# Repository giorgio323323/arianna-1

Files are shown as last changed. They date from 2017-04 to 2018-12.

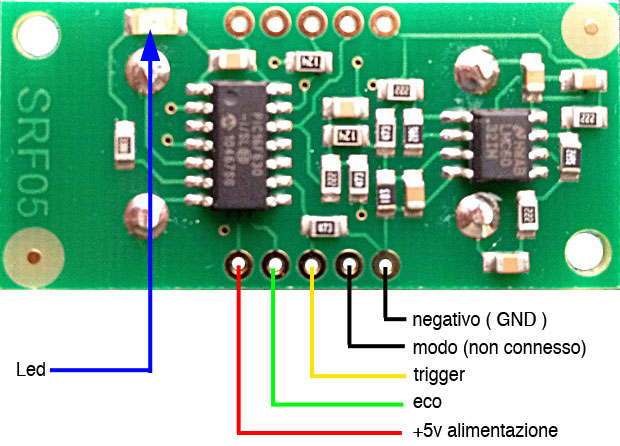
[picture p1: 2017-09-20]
hw/sensore-ad-ultrasuoni-srf.05jpg.jpg

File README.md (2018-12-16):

# Arianna
Arianna: il robot biblitecario.

il progetto è stato portato in: https://github.com/giorgio323323/ARI_V3

## Introduzione

Da [Arianna by CSBNO](http://webopac.csbno.net/library/Canegrate/makers-lab/arianna/) :
> Arrivo in biblioteca e chiedo “Robinia Blues” di Valter Binaghi, il bibliotecario consulta il computer e mi informa che c’è e lo posso trovare tra gli autori italiani. Un attimo di imbarazzo, non frequento questo luogo abbastanza da conoscere la disposizione degli scaffali, faccio per domandare ma il mio interlocutore mi anticipa dicendomi di seguire Arianna. Arianna? Un sibilo mi fa voltare, vedo una macchinina che parte lungo il corridoio, porta la scritta Arianna. Al mio sguardo interrogativo il mio interlocutore mi fa cenno di andare, segua Arianna mi dice. Tutto dura pochi secondi nei quali valuto anche la possibilità di essere vittima di “Scherzi a parte”, Arianna si ferma, si gira un poco e con un altro fruscio un puntatore luminoso si muove, si accende e quando decido di guardare dove Arianna sembra “indicare” vedo una luce sui libri e li vicino il mio “Robina Blues”. Lo prendo, lo sfoglio e me ne vado un poco stupito, saluto il bibliotecario e nel frattempo risento il sibilo. Vedo Arianna che torna da dove era venuta, la vedo accoccolarsi in una piccola casetta e io lascio la biblioteca pronto a rileggere il libro di un bravo insegnante che ha attraversato i nostri luoghi.

## Obiettivo 
La costruzione di un robot ***autonomo*** ed ***indipendente*** con lo scopo di accompagnare una persona al libro richiesto. La navigazione avviene in un ambiente dinamico dove anche i singli scaffali possono cambiare di posizione.

## Roadmap

- [x] Start
- [x] Primi prototipi (Ambros,Arianna,4rianna,..)
- Struttura
    - [ ] Arianna
    - [ ] Ambros
    - [ ] 4rianna
    - [ ] ..
- Movimento
    - [ ] Motori DC
    - [x] Stepper
    - [ ] Altro
- Altro
- [ ] Interazione biblio DB

## Contatti
[STUFFcube](https://stuffcube.wordpress.com/)

## License

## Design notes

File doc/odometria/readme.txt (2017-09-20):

Introduction to the files in the Kalman filter simulator .zip file.

After you have unpacked the .zip file you have obtained a directory that contains the Matlab simulator functions that I've used in my thesis on Robot Localization and Kalman Filters. All plots presented in the thesis are generated using the functionality of the simulator.

The simulator does not have a graphical user interface. You will have to look into the different function files to get to know the workings of the simulator, although I don't think that that will give many problems. 

charts/ contains functions to plot charts when data is generated
diff_drive/ contains the truth and KF model that implement the drive system and sensor models from the thesis. In particular, diff_drive_problem.m defines the estimation problem. This file is documented with comments on how to use the file.
kf_methods/ contains functions that implement different KFs
misc/ contains miscalaneous functions needed by the simulator
track_drive_single_and_multiple/ contains the models used when detecting single or multiple landmarks at the same time

To get started, make sure that the pathdef.m includes the subdirectories in this directory. 
Then either run 'demo_fs_ekf' (extended Kalman Filter) or 'demo_fs_iekf' (iterated extended Kalman filter).

To get to know the simulator, it is easiest to try the above commands and step through each line of the code. I have added commentry to the code to make it more understandable. However, if you have questions, feel free to contact me via http://contact.negenborn.net/.

Rudy Negenborn
http://www.negenborn.net/

August 2003
July 2009 (update)

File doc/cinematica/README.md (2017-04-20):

# Cinematica

Qui puoi trovare i contenuti per la gestione del movimento dei motori di [Arianna].
>La cinematca è quel ramo della meccanica che si occupa di descrivere quantitativamente il moto dei corpi, indipendentemente dalle cause del moto stesso.

In pratica qui vengono approfonditi come muovere arianna, nonchè formule e ragionamenti che hanno portato a certe soluzioni.

Qui si trovano file per la gestione dei movimenti attraverso motori. Per ora viene contemplato solo l'utilizzo di motori stepper, in futuro verranno mergiati nuovi esempi con motori DC.

#Obiettivi
- [x] Init
- [ ] Gestione degli stepper
  - [x] Gestione accelerazione e velocità (tramite [https://github.com/adafruit/AccelStepper](AccellStep by LadyAda)
  - [x] Buy ingredients
  - [ ] Cook recipe
- [ ] Sleep

# Esempi

La seguente cartella contiene alcuni esempi di utilizzo di stepper con alcune librerie vedi
  - Import a HTML file and watch it magically convert to Markdown
  - Drag and drop images (requires your Dropbox account be linked)

#Dipendenze

Attenzione!
Il seguente codice riporta delle dipendenze, installale o verifica la presenza nel tuo ambiente prima di compilare il codice.

| Dipendenza | IDE |
| --- | --- |
| [AccelStepper](https://github.com/adafruit/AccelStepper) | Arduino |
| [AFMotor](https://github.com/adafruit/Adafruit-Motor-Shield-library) | Arduino |

Tips:
  - Installa scaricando la repo da Zip, si fa prima ;).

### Todos

License
----

MIT

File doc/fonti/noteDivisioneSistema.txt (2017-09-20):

note sulla divisione del sistema Arianna

il sistema è suddiviso su tre parti logiche e volendo anche hardware

lo chiamo Attuatore, anche se il termine può essere improprio: 
	si occupa della gestione dei sensori e degli attuatori. 
	
	un Arduino controlla la velocità, direzione, misura lo spostamento delle ruote.
	legge i sensori di distanza dagli oggetti.
	governa il sensore di puntamento del libro.
	restituisce informazioni sul suo stato.

	ha delle funzioni primitive che vengono comandate via seriale da un livello superiore

	ho trovato che delle primitive utili sono:

		movimento con arresto al superamento della Distanza obbiettivo
			il movimento può essere:
				con direzione imposta dal supervisore scrivendo angolo di sterzo 
				con direzione controllata in modo da stare a a una certa distanza dalla
				parete sx o dx. Il controllo regola lo sterzo
				per mantenere la parete a una certa distanza.
		
		definire la velocità di crociera
		definire la distanza da percorrere
		
		nel mio caso ho montato un sensore a ultrasuoni sul frontale. Posso ruotarlo
		a piacere con un servo (PAN). da qui i comandi A e m.
		Sul PAN c'è un servo che fa il TILT del puntatore.
		Giunti allo scaffale il robot arretra curvando per allontanarsi dallo scaffale.
		L'incertezza della fermata la correggo effettuando delle misure della distanza
		dalla libreria, la minima distanza indica che il sensore (PAN) è perpendicolare.
		In base alla distanza dalla libreria e all'altezza del ripiano calcolo l'angolo
		di TILT e così posso puntare.
		
		lo script farebbe:
		riceve dati da Interfaccia (vedi sotto)
		comando moto con sensore sx per una distanza D = Dscaffale
		all'arresto moto con sterzo imposto e distanza D = -distanza di arrestramento
		algortimo di ricerca m minima in funzione dell'angolo
		invio angolo di TILT in funzione di m trovata e altezza ripiano
		accendi puntatore
		
		voilà, le jeux sont fait

			S Scrivo sterzo e suo angolo						[gradi] 90 diritto 
																		180 dx
																		0   sx
			D scrivo distanza relativa da percorrere e valore 	[mm]
			d lettura distanza assoluta (odometro)				[mm]
			V scrivo setpoint velocita' con valore motorSpeedValue
			v leggo velocità (motorSpeedRef)
			e errore
			l libero (viaLibera) stato sensore anteriore
			r statoRun	
			R statoRun (scrivi) 0: fermo, 1: controllo con sensore dx, 2: sterzo esterno
			  si ferma al superamento quando odometro supera la D attiva 
			A angolo sonar
			m misura con sonar [cm]

Supervisore, anche questo termine può essere rivisto: 
	tramite seriale comanda le primitive dell'attuatore per comporle in movimenti organici e complessi.
	riceve indicazioni su cosa fare dall'Interfaccia con la biblioteca

Interfaccia, è un software che gira sul pc della biblioteca. 
	A partire dal codice del libro interroga il dataBase che restituisce un record contenente:
	numero scaffale
	numero ripiano
	posizione x, y, z del centro del ripiano dove giace il libro
	
	Passa queste informazioni al SUpervisore.
	
	questo DB deve essere popolando manualemnte censendo i ripiani della biblioteca e individuando il libri 
	posti agli estremi del ripiano.
	
	il nostro scopo non è puntare il libro ma il ripiano che lo contiene.

La comunicazione tra Attuatore e Supervisore

	Avviene tramite seriale. Indipendentemente da come verrà fatto il supervisore (Raspberry, ESP, altro) 
	ho trovato comoda una interfaccia a misura "umana", cioè con stringhe di comando mnemoniche, un poco tipo
	Gcode. Questo permette di testare il sistema con una interfaccia seriale testuale (es quella nell'IDE
	di Arduino).
	Dispone di un semplice l'acknowledge di ricezione comando e un timeout.
	
	Sul supervisore si possono realizzare dei semplici script che sfruttano le funzioni base per
	farne di complesse.
	
	Se concordiamo di renderla comune possiamo condividere diverse cose. 
	
	metto in fondo lo snippet di codice che la realizza e descrive:

// 

	/*
	verifica se arrivano caratteri da seriale
	considero un pacchetto con la forma char1 (comando) seguito da un eventuale parametro
	In maiscolo i valori che scrivo
	in minuscolo quelli che leggo
	
	char 1:	parametro modificato, 
			S Scrivo sterzo e suo angolo						[gradi] 90 diritto 
																		180 dx
																		0   sx
			D scrivo distanza relativa da percorrere e valore 	[mm]
			d lettura distanza assoluta (odometro)				[mm]
			V scrivo setpoint velocita' con valore motorSpeedValue
			v leggo velocità (motorSpeedRef)
			e errore
			l libero (viaLibera) stato sensore anteriore
			r statoRun	
			R statoRun (scrivi) 0: fermo, 1: controllo con sensore dx, 2: sterzo esterno
			  si ferma al superamento quando odometro supera la D attiva 
			A angolo sonar
			m misura con sonar [cm]

*/

void getCmd(void){
static float x, y;
static char smComandi = 0;
static char inCmd;
static unsigned long time, cmdTime;

	// se il pacchetto non arriva completo in un secondo 
	// resetto ricezione
	if ((smComandi != 0) && ((millis() - cmdTime) > 1000 )) {
		Serial.println('Timeout');
		smComandi = 0;
	}

	if (Serial.available() > 0) {

		switch (smComandi) {
			case 0: // attesa 1rst valore

				inCmd = Serial.read();
				cmdTime = millis();
				
				switch (inCmd) {
		
					// scrivo valore
					case 'S': 
					case 'D': 
					case 'R': 
					case 'V': 
					case 'A': 
							smComandi = 1;		// stato a seconda del numero di
												// parametri da ricevere
						break;
		
					case 'd': 
					case 'e': 
					case 'v': 
					case 'l': 
					case 'r': 
					case 'm': 
							smComandi = 2;		// stato a seconda del numero di
												// parametri da ricevere
												// questa è lettura quindi segue subito risposta
						break;
				}
				break;
			case 1: // attende 1 valore
				// look for the next valid integer in the incoming serial stream:
				x = Serial.parseInt();
				smComandi = 2; 	// mette in esecuzione valore
				break;	
				
			case 2: // attesa terminatore

				if (Serial.read() != '\n') break;
				
				switch (inCmd) {
					case 'S': 
							angoloSterzo = x;
							smComandi = 0;		
							Serial.print("S: ");
							Serial.println(angoloSterzo);
						break;
		
					case 'D': 
							distanza += x;
							smComandi = 0;		
							Serial.print("D: ");
							Serial.println(distanza);
						break;
		
					case 'R': 
							statoRun = x;
							smComandi = 0;		
							Serial.print("R: ");
							Serial.println(statoRun);
						break;

					case 'V': 
							motorSpeedValue = x;
							smComandi = 0;		
							Serial.print("V: ");
							Serial.println(motorSpeedValue);
						break;
		
					case 'A': 
							sonarAngle = x;
							smComandi = 0;		
							Serial.print("A: ");
							Serial.println(sonarAngle);
						break;
		
					case 'd': 
							smComandi = 0;		
							Serial.print("d: ");
							Serial.println(odometro);
						break;
		
					case 'e': 
							smComandi = 0;		
							Serial.print("e: ");
							Serial.println(errore);
						break;
		
					case 'v': 
							smComandi = 0;		
							Serial.print("v: ");
							Serial.println(motorSpeed);
						break;

					case 'l': 
							smComandi = 0;		
							Serial.print("l: ");
							Serial.println(viaLibera);

					case 'r': 
							smComandi = 0;		
							Serial.print("r: ");
							Serial.println(statoRun);
						break;

					case 'm': 
							smComandi = 0;		
							misura = sonarMisura(5);
							Serial.print("m: ");
							Serial.println(misura);
						break;
				}
				
				break;
			default:
				smComandi = 0;
				break;
		}
		
	}// in serialLine.available
}

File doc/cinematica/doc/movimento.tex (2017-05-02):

\documentclass[12pt,oneside,a4paper]{article}

%% Language and font encodings

\usepackage[english]{babel}
\usepackage[utf8x]{inputenc}
\usepackage[T1]{fontenc}
\usepackage{amssymb,tikz,pdftexcmds,xparse}

%change caption of contents e appendices

\addto\captionsenglish{% Replace "english" with the language you use
	\renewcommand{\figurename}{Figura}%
	\renewcommand{\contentsname}{Table of Contents}%
	\renewcommand{\contentsname}{Contenuti}
}

%% Give you the possibiliy of split text
\usepackage{seqsplit}

%% Sets page size and margins
\usepackage[a4paper,top=3cm,bottom=2cm,left=3cm,right=3cm,marginparwidth=1.75cm]{geometry}

%%allow to break url
\usepackage[hyphens]{url}

%% Useful packages
\usepackage{amsmath}
\usepackage{graphicx}
\graphicspath{ {./immagini/} }
\usepackage[colorinlistoftodos]{todonotes}
\usepackage[colorlinks=true, allcolors=black]{hyperref}
\usepackage{todonotes}
\usepackage{multicol}

%appendice 
\usepackage[toc,page]{appendix}
\renewcommand\appendixtocname{Appendice}
\renewcommand\appendixpagename{Appendice}
%% Personal function

%no label
\usepackage[nolabel, final]{showlabels}

%% Solidity env, per ora è java
\usepackage{listings}
\usepackage{color}

\definecolor{dkgreen}{rgb}{0,0.6,0}
\definecolor{gray}{rgb}{0.5,0.5,0.5}
\definecolor{mauve}{rgb}{0.58,0,0.82}

\lstset{frame=tb,
	language=Java,
	aboveskip=3mm,
	belowskip=3mm,
	showstringspaces=false,
	columns=flexible,
	basicstyle={\small\ttfamily},
	numbers=none,
	numberstyle=\tiny\color{gray},
	keywordstyle=\color{blue},
	commentstyle=\color{dkgreen},
	stringstyle=\color{mauve},
	breaklines=true,
	breakatwhitespace=true,
	tabsize=3
}

	\title{Movimento di un robot 2 motori rear e una sfera front}
	\author{Luca Vecchi - STUFFCUBE}
	\date{20 Aprile 2017}

\begin{document}
	%\input{./Struttura/Frontespizio.tex}

	\maketitle
	\clearpage

	%	\input{Struttura/Introduzione.tex}
	
	\section{Curvatura}
	
	Vogliamo astrarre il movimento di Arianna in due tipologie diverse: rette e circonferenze. Una futura implementazione delle curve bezier (manca di trovare come fare l'offset e di modificare il path) potrà dare una completa gestione dei movimenti potendo controllare anche l'angolo di arrivo al punto.
	
	Possiamo considerare il contenuto informativo di $S_0 \bigcup r_0$ al pari di $\alpha \bigcup r_0$ e $S_0 \bigcup \alpha$ per via delle ovvie uguaglianze.
	Nel nostro caso per le rette andremo a definire la funzione \textit{Retta} come segue:
	retta ($S_0$): $S_s , S_d$
	
	, mentre nel caso delle circonferenze:
	
	circ($\alpha$,$r_o$,$\Delta$):  $S_s , S_d$
	
	dove $\delta$ è la distanza tra il centro del robot e la circonferenza tracciata dal movimento del centro delle ruote.
	
	\begin{equation*}
	S_0 \equiv \alpha * 2 * \pi * r_0 \div 360
	\end{equation*}
	\begin{equation*}
	S_1 \equiv \alpha * 2 * \pi * (r_0 - \Delta) \div 360
	\end{equation*}	
	\begin{equation*}
	S_2 \equiv \alpha * 2 * \pi * (r_0 + \Delta) \div 360
	\end{equation*}
	
	Come si evince dall'immagine \ref{fig:circonferenze} si può notare le circonferenze concentriche, rappresentate dalla più interna verso l'esterna, come il tragitto effettuato dalla ruota più interna, dal centro del robot e dalla ruota più esterna.
	
	La difficoltà sta nella gestione dei motori in modo sincrono in quanto perchè il centro del robot effettui una circonferenza perfetta, la velocità delle ruote deve essere mantenuta costante\footnote{Vedi libreria Accelstepper}.

	\clearpage

	%% Bibliography .bib
	%\bibliography{./Struttura/bib.bib}
	%\bibliographystyle{unsrt}	
\end{document}

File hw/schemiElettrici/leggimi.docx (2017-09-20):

https://www.build-electronic-circuits.com/gerber-file/

HC-06 Bluetooth module

http://42bots.com/tutorials/hc-06-bluetooth-module-datasheet-and-configuration-with-arduino/

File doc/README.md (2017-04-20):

# Testo

Qui si potrebbe inserire un testo riassuntivo per la produzione di un ***pdeffone*** enorme che conterrà tutto il percorso.

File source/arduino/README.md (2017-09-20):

# arianna
arianna: il robot biblitecario

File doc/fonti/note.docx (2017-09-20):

Arrivo in biblioteca e chiedo “Robinia Blues” di Valter Binaghi, il bibliotecario consulta il computer e mi informa che c’è e si trova tra autori italiani. Un attimo di imbarazzo, non frequento questo luogo abbastanza da conoscere la disposizione degli scaffali, faccio per domandare ma il mio interlocutore mi anticipa dicendomi di seguire Arianna. Arianna ? Un sibilo mi fa voltare, vedo una macchinina che parte lungo il corridoio, porta la scritta Arianna. Al mio sguardo interrogativo il mio interlocutore mi fa cenno di andare, segua Arianna mi dice. Tutto dura pochi secondi nei quali valuto anche la possibilità di essere vittima di “Scherzi a parte”, Arianna si ferma, si gira un poco e con un altro fruscio un puntatore luminoso si muove, si accende e quando decido di guardare dove Arianna sembra “indicare” vedo una luce sui libri e li vicino il mio “Robina Blues”. Lo prendo, lo sfoglio e me ne vado perplesso, saluto il bibliotecario e nel frattempo risento il sibilo. Vedo Arianna che torna da dove era venuta, la vedo accoccolarsi in una piccola casetta e io lascio la biblioteca pronto a rileggere il libro di un bravo insegnante che ha attraversato i nostri luoghi.

Arianna è un robot che è in grado di muoversi sul pavimento e andare dove gli viene richiesto. E’ il progetto che abbiamo avviato all’interno di StuffCube. La prima parte è stato definire cosa deve fare, lo abbiamo descritto nell’incipit. Successivamente abbiamo scomposto il progetto nelle diverse funzioni di considerando le caratteristiche della biblioteca che ci ospita:

- Realizzare oggetto che si muove (rover cioè vagabondo)
- sensori sul rover
- ricevimento comandi di destinazione
- determinare dove deve andare
- determinare dove è
- determinare il moto verso la destinazione
- indicare il libro
- ritorno a casa
- ricarica
- mappare gli scaffali quando vengono spostati.

Altri vincoli di progetto che ci siamo dati sono di essere il meno intrusivi possibile, questo fa si che dobbiamo evitare soluzioni che richiedano sorgenti di alimentazione, oppure il porre strisce guida sul pavimento e cosi via.

Inizieremo partendo dagli scaffali più semplici, quelli che affiancano la parete. L’idea è seguire lo scaffale viaggiandoci radente e identificando dove siamo misurando lo spostamento e usando dei segni già presenti sulla struttura. Guardare cosa hanno fatto altri è utile e istruttivo.

questi post sono il diario di questo progetto così come si sviluppa. Se la cosa ti interessa non esitare, manda una mail e vienici a trovare.

Nel nostro caso abbiamo un punto di partenza noto e delle informazioni riguardo allo spostamento e alla velocità di spostamento.

Questi si integrano (data fusion) con gli altri.

Scomposizione del problema:

- Realizzare oggetto che si muove (rover)
- sensori sul rover
- determinare dove deve andare
- determinare dove è
- determinare il moto
- mappare gli scaffali quando mossi. RFID con antenna potente ()
- ritorno a casa
- ricarica
- ricevimento comandi di destinazione
- indicare il libro

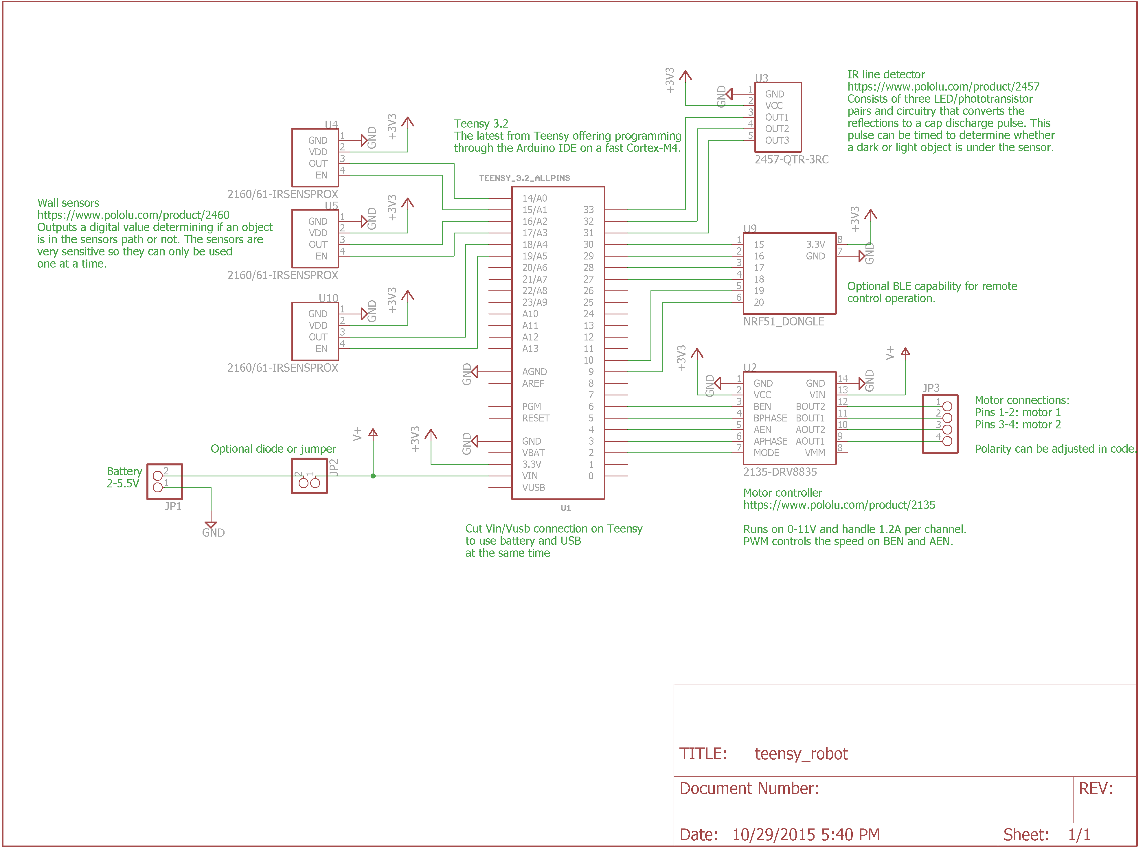
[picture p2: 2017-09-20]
doc/fonti/robot_schematic_.png

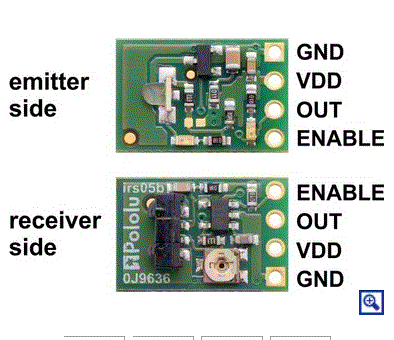
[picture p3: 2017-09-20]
hw/Pololu 38 kHz IR Proximity Sensor 2579.GIF

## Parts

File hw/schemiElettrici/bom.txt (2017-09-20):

Partlist

Exported from shieldAtmegaArianna_00.brd at 18/06/2017 21:36:41

EAGLE Version 6.5.0 Copyright (c) 1988-2013 CadSoft

Assembly variant: 

Part          Value          Package      Library  Position (mil)        Orientation

ADCH          J_ADCH         1X08         pinhead  (3250 100)            R0
ADCL          J_ADCL         1X08         pinhead  (2350 100)            R0
BT_BOARD      J_ESP          1X04         pinhead  (3260 1235)           R90
C1            100nF          C050-025X075 rcl      (570 1070)            R0
C3            100nF          C050-025X075 rcl      (2215 1080)           R0
C4            100nF          C050-025X075 rcl      (1575 360)            R0
C5                           E5-8,5       rcl      (1085 310)            R90
COMMUNICATION J_COMM         1X08         pinhead  (3050 2000)           R180
ENC_DX        J_ENC_DX       1X03         pinhead  (2890 855)            R90
ENC_SX        J_ENC_SX       1X03         pinhead  (2895 455)            R90
ESP_BOARD     J_ESP          1X04         pinhead  (275 1790)            R0
IC1           74AC00N        DIL14        74xx-eu  (555 640)             R270
IC2           74AC14N        DIL14        74xx-eu  (2215 625)            R270
ICSP          ICSP           2X03         pinhead  (2555 1100)           R270
ICSP1         ICSP           2X03         pinhead  (720 1820)            R180
JP1                          1X01         pinhead  (3700 2000)           R0
JP2                          1X01         pinhead  (3800 2000)           R0
JP3                          1X01         pinhead  (3700 300)            R0
JP4                          1X01         pinhead  (3800 300)            R0
LASER         J_LASER        1X02         pinhead  (1640 1615)           R90
L_SIDE_IR     J_L_SIDE_IR    1X04         pinhead  (205 1075)            R90
MTR_A         j2             1X02         pinhead  (1040 975)            R90
MTR_B         J1             1X02         pinhead  (1040 695)            R90
POWER         J3             1X06         pinhead  (1550 100)            R0
PWMH          J4             1X08         pinhead  (1290 2000)           R180
PWML          J5             1X08         pinhead  (2150 2000)           R180
R1            220            0207/10      rcl      (2700 1775)           R0
R2            330            0207/10      rcl      (2700 1665)           R180
R3            220            0207/10      rcl      (3075 1600)           R90
R4            330            0207/10      rcl      (3075 1115)           R90
R7            10k            0207/10      rcl      (1800 1050)           R90
R8            220            0207/10      rcl      (2450 1470)           R180
R9            2200           0207/10      rcl      (2455 1350)           R180
R10           220            0207/10      rcl      (2685 680)            R90
R11           2200           0207/10      rcl      (2570 680)            R90
R_SIDE_IR     J6             1X04         pinhead  (195 435)             R90
SNR_REAR      J7             1X04         pinhead  (275 1480)            R0
SRV_PAN       J8             1X03         pinhead  (3250 490)            R90
SRV_TILT      J10            1X03         pinhead  (3445 490)            R90
U$1           DRV8803        8X5CARRIER   arianna  (1455 995)            R180
XIOH          J11            2X08         pinhead  (3750 1550)           R90
XIOL          J12            2X08         pinhead  (3750 750)            R90

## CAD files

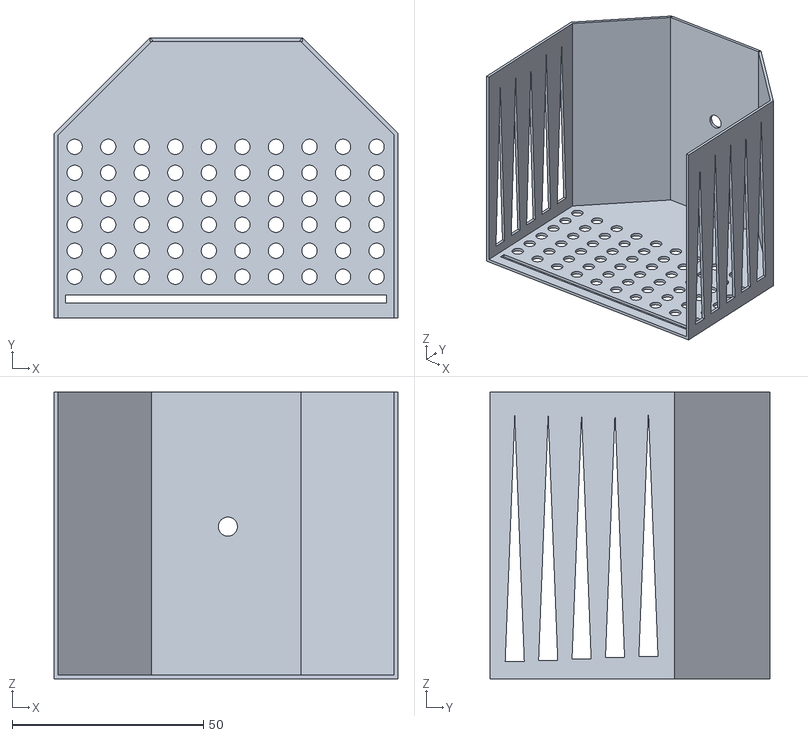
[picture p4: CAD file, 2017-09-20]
hw/3d/Component2.stl
90.0 x 73.3 x 75.0

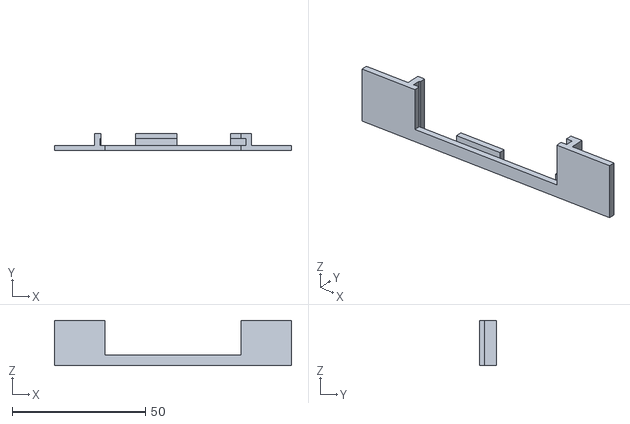
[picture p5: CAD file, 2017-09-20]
hw/3d/supportoATmegaFront.stl
89.0 x 6.50 x 17.0

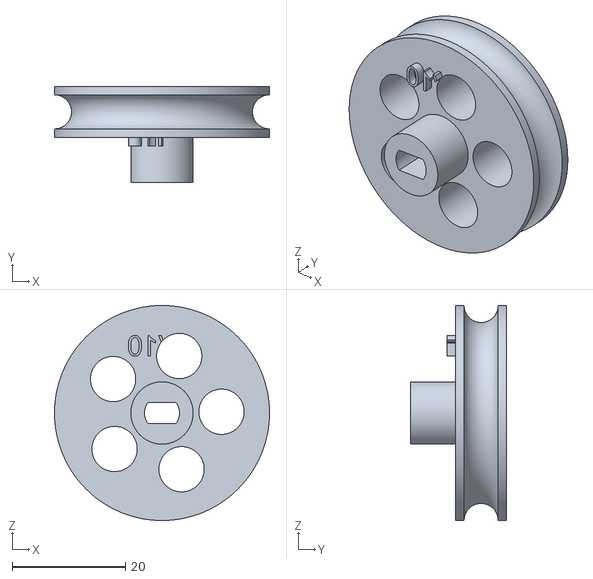
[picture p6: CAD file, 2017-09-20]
hw/3d/ruotaMotricePiccola v11.stl
38.0 x 17.0 x 38.0

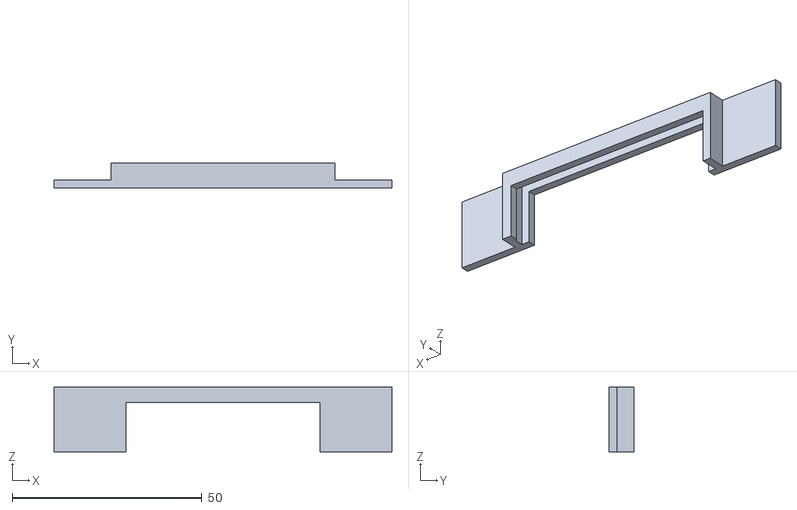
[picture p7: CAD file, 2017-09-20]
hw/3d/supportoATmegaDietro.stl
89.0 x 6.50 x 17.0

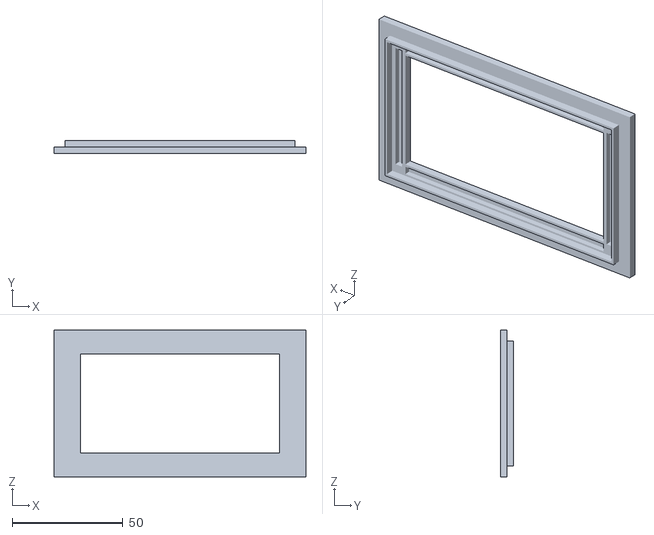
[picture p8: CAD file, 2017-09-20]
hw/3d/atMegabottom.stl
114.0 x 6.00 x 66.5

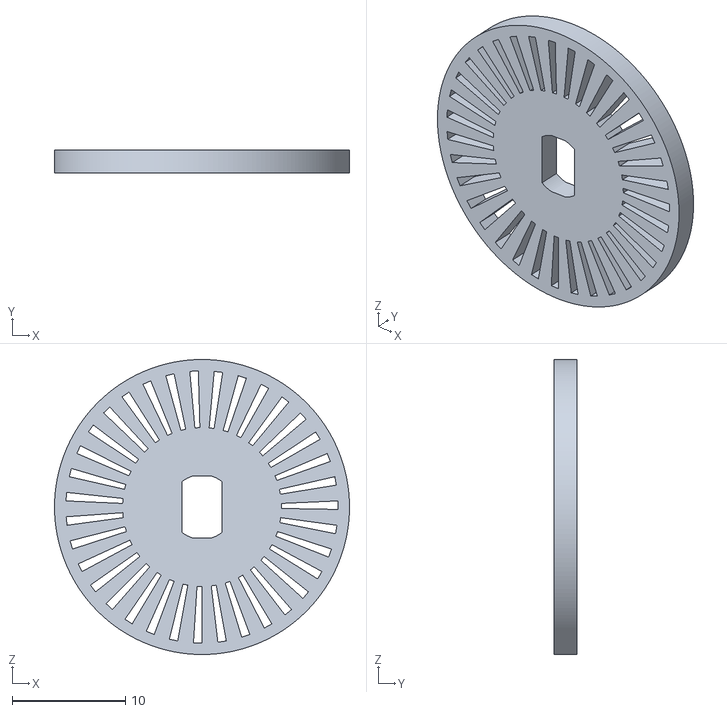
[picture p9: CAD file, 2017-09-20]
hw/3d/encoder.stl
26.0 x 2.00 x 26.0

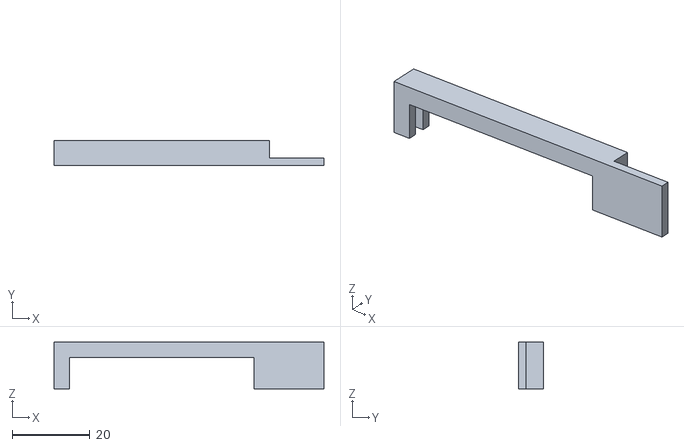
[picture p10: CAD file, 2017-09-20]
hw/3d/supportoBasetta51mm v1.stl
69.4 x 6.50 x 12.0

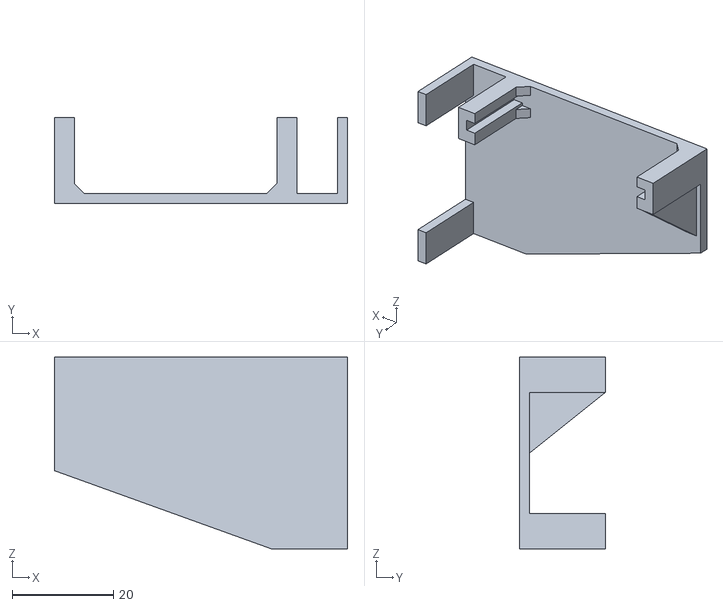
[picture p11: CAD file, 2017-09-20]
hw/3d/supportoSonarLaser v5.stl
58.0 x 17.0 x 38.0

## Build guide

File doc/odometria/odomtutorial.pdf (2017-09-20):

# A Primer on Odometry and Motor Control

Edwin Olson

December 4, 2004

### 1 Introduction

Most robotics problems ultimately reduce to the question: where am I? How can you go somewhere else without some notion of where you are now? You could proceed naively, stumbling around, hoping that your goal will appear in range of your robot’s sensors, but a better plan is to navigate. A basic method of navigation, used by virtually all robots, is odometry, using knowledge of your wheel’s motion to estimate your vehicle’s motion.
The goal of this primer is to show you how to use odometry data. A real dataset will be used extensively to show how well (and how badly) these ideas can work.
Suppose your robot starts at the origin, pointed down the xaxis. Its state is (x, y, θ) = (0, 0, 0). If the robot travels (roughly) straight for three seconds at 1 m/s, a good guess of your state will be (3, 0, 0). That’s the essence of odometry.
We’ll assume that the vehicle is differentially driven: it has a motor on the left side of the robot, and another motor on the right side. If both motors rotate forward, the robot goes (roughly) straight. If the right motor turns faster than the left motor, the robot will move left.
Our goal is to measure how fast our left and right motors are turning. From this, we can measure our velocity and rate of turn, and then integrate these quantities to obtain our position.

### 2 Derivation

The speeds of our motors give us two quantities: the rate at which the vehicle is turning, and the rate at which the vehicle is moving forward. All we have to do is integrate these two quantities, and we’ll have our robot’s state (x, y, θ).
That sounds a bit scary, but the mathematics end up being very simple. If we had analytic expressions for the angular rate and forward rate functions, their integral probably would be scary. But in a real system, our data comes from real sensors that are sampled periodically. Every few milliseconds, we get a new measurement of our motor velocities. We will numerically integrate our solution, which is of course, just a fancy way of saying that we’ll divide time up into little chunks and just add up all the little pieces.
Suppose our robot is at (x, y, θ). Depending on what kind of sensors we have, we might get measurements of how much the motors have rotated (in radians), or an estimate of how fast they’re rotating (angular rate, radians/sec.) We’ll consider the first case, but of course the second case can be handled by just multiplying the angular rate by the amount of time that has elapsed since our last iteration. Given the amount of rotation of the motor and the diameter of the wheel, we can compute the actual distance that the wheel has covered.

Suppose the left wheel has moved by a distance of dleft and the right wheel has moved dright. For some small period of time (such that dleft and dright are short), we can reasonably assume that the vehicle trajectory was an arc (see Fig. 1).

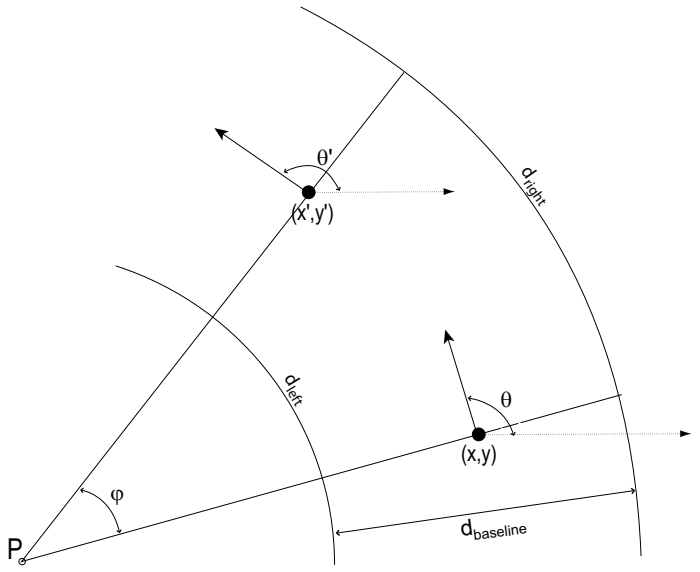
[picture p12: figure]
dright; dleft; dbaseline

Figure 1: Odometry geometry. Over a small time period, the robot’s motion can be approximated by an arc. The odometry problem is to solve for (x

, y

, θ
) given (x, y, θ) and
dbaseline. In the figure, the robot is moving counterclockwise.

The initial state (x, y, θ) defines our starting point, with θ representing the vehicle’s heading. After our vehicle has moved by dleft and dright, we want to compute the new position, (x

, y

, θ
).
The center of the robot (the spot immediately between the two wheels that define’s the robot’s location), travels along an arc as well. Remembering that arc length is equal to the radius times the inner angle, the length of this arc is:
dleft + dright dcenter = | (1) 2

Given basic geometry, we know that:

φrleft = dleft | (2)
φrright = dright | (3)

If dbaseline is the distance between the left and right wheels, we can write:

rleft + dbaseline = rright | (4)
Subtracting (2) from (3), we see:

φrright − φrleft = dright − dleft

φ(rright − rleft) = dright − dleft

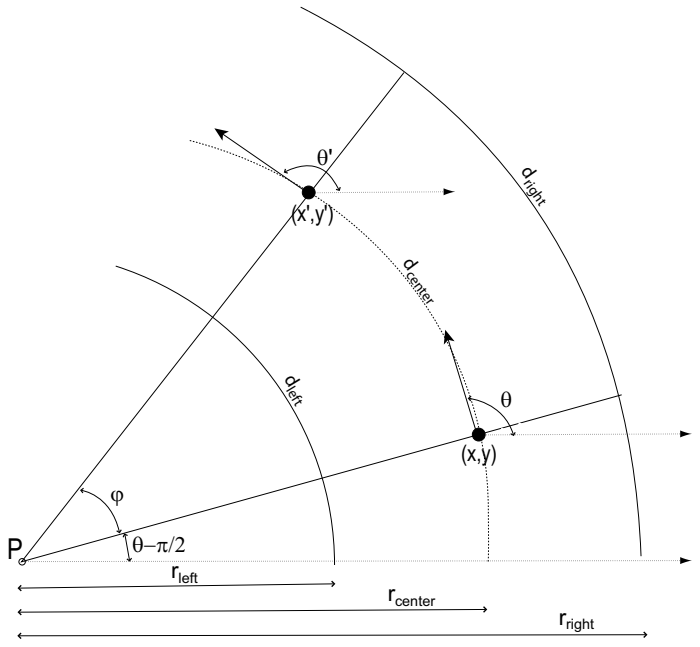
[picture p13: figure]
dright; d center; dleft; rleft; rcenter; rright

Figure 2: Detailed odometry geometry. We compute the center of the circle P by forcing dleft and dright to be two arcs with the same inner angle φ. From this, we can compute the new robot position (x

, y

, θ
).

φdbaseline = dright − dleft

dright − dleft φ = | (5) dbaseline

At the risk of making the math a bit uglier than really necessary, let’s very carefully compute the new robot state. All of our arcs have a common origin at point P. Note that the angle of the robot’s baseline with respect to the x axis is θ − π/2. We now compute the coordinates of P:

Px = x − rcentercos(θ − π/2) = x − rcentersin(θ)
Py = y − rcentersin(θ − π/2) = y + rcentercos(θ)

Now we can compute x and y :

x = Px + rcentercos(φ + θ − π/2)
= x − rcentersin(θ) + rcenter ∗ sin(φ + θ)
= x + rcenter[−sin(θ) + sin(φ)cos(θ) + sin(θ)cos(φ)] | (6)

and y = Py + rcentersin(φ + θ − π/2)
= y + rcentercos(θ) − rcentercos(φ + θ)
= y + rcenter[cos(θ) − cos(φ)cos(θ) + sin(θ)sin(φ)] | (7)

If φ is small (as is usually the case for small time steps), we can approximate sin(φ) = φ and cos(φ) = 1. This now gives us:

x = x + rcenter[−sin(θ) + φcos(θ) + sin(θ)]
= x + rcenterφcos(θ)
= x + dcentercos(θ) | (8)

and

y = y + rcenter[cos(θ) − cos(θ) + φsin(θ)]
= y + rcenter[φsin(θ)]
= y + dcentersin(θ) | (9)

In summary, our odometry equations for (x

, y

, θ
) reduce to:
dleft + dright dcenter | = | (10) 2
dright − dleft φ = | (11) dbaseline
θ | = θ + φ | (12)
x | = x + dcentercos(θ) | (13)
y | = y + dcentersin(θ) | (14)

### 3 Basic Motor Theory

Subsequent sections will discuss how we can measure the performance of our motors. We’ll need to put this into context by talking first about some basic motor physics.
Motors are devices which manipulate magnetic fields in order to convert electrical energy into rotational energy. An electric current flows through coils of wire, causing a magnetic field to form. This magnetic field interacts with permanent magnets (like those on your refrigerator), causing the shaft to rotate.
We also know that motors can be used in reverse; if you rotate the shaft of the motor, the permanent magnets induce a current in the rotating coils of wire. This, of course, is known as a generator.
It is important to realize that motors are always behaving as generators. If the output shaft is rotating, a current is being induced in the wires. Usually, this current opposes the current resulting from an externally applied voltage.

### 3.1 Motor model

A motor can be simply modelled by the resistance of its coil of wire and a voltage source that produces a voltage proportional to rotational speed (see Fig. 3). The “generator” voltage

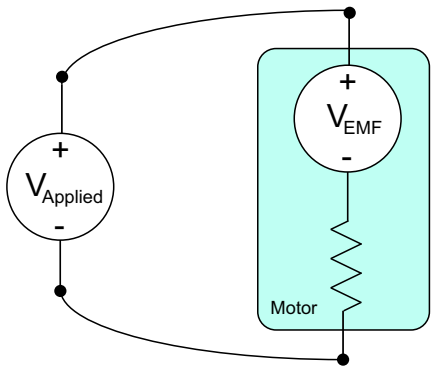
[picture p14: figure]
VEMF; VApplied; Motor

Figure 3: Simple motor model. The simplest motor model is a resistor (corresponding to the resistance of the motor’s wire coil), and a voltage source corresponding to the Back EMF.

is known as the Electro-Motive Force (EMF). It’s often called the “Back EMF”, since it’s the voltage coming back out of the motor.
When we interface with a motor, we typically control the voltage applied to the motor. This applied voltage can cause current to flow into the motor. At any given moment, Ohm’s law can be applied. However, the voltage that we have to consider isn’t the applied voltage, but the net voltage: Vapplied − Vemf . In other words, the current can be written:
I = (Vapplied − Vemf )/Rwinding | (15)
The current of a motor is extremely important: it is proportional to the torque. A motor only does work when its producing torque, and since torque is proportional to current, this only occurs when Vapplied = Vemf .
When a voltage is first applied to a motor, Vapplied − Vemf > 0, and so current will flow. This will produce torque and the output shaft will begin to rotate (provided the torque exceeds the static friction of the load.) As time goes on, the motor will slowly accelerate. As the motor gains speed, Vemf increases, and the current drops. At some point, we’ll reach an equilibrium, where the motor’s torque (and current) exactly matches the load.
Here’s an important thought experiment: suppose we take a motor and short the two leads together. Will it be easier or harder to turn the output shaft? If we turn the output shaft, the motor will act as a generator, producing a voltage of Vemf . But the applied voltage is zero, since the leads are shorted. All of the back EMF voltage is applied across the motor winding, inducing a current. This current will generate a torque that will oppose the external torque. Setting both terminals of a motor to the same voltage brakes the motor, without the need for any mechanical mechanism.

### 3.2 Applied Voltage and PWM

As we’ve seen, the applied voltage is intimately involved in the behavior of a motor. Special circuitry is required to drive motors; a typical microcontroller can only provide a very small amount of power on each of its outputs– far too little to power a motor. We’ll need some additional circuitry to drive the motors.
It turns out that building a circuit that can output an arbitrary applied voltage at high current is quite difficult. It is much easier to build a simple high current switch, whose output is either Vmax or zero. In fact, we can build a switch that can change state very fast, upwards of 100kHz.

period

50%

20%

80%

Suppose you’re trying to build a dimmable light switch; can you build one from just an onoff switch? Suppose you start flipping the light on and off repeatedly, at first fairly slowly. The room is bright, then dark, then bright again. Not a very good dimmer! But you can probably imagine that if you could flip the switch fast enough, that you could achieve intermediate brightness levels. This is what we’re going to do with motors.
If the switch is “on” 50% of the time, you might expect the motor to run about the same as it does at 50% the voltage. This does, in fact, work... provided that the switching is fast enough. The criteria for the switching rate is that the voltage has to change faster than the motor can react; the motor has an “electrical time constant”, which reflects how rapidly it can react to changing electrical conditions.

Figure 4: PWM Waveforms. We can approximate different applied voltages by using a pulsewidthmodulated signal whose period is less than the motor’s electrical time constant.

This technique is called Pulse Width Modulation (PWM) (see Fig. 4), since the width of each pulse is modulated in order to approximate different values of Vapplied.
In general, motor electrical time constants are on the order of a few milliseconds, but PWM frequencies in the ¡20kHz range can cause audible vibrations. So often, PWM frequencies are increased well above the human range of hearing.

### 3.3 Deficiencies of our model

This is a pretty good model for a motor, but it ignores one often important detail: electrical transients. When the motor is in steady state (i.e., it’s been rotating under a uniform load for a long time), our model is accurate. But when conditions are changing (the load is changing, or the applied voltage is changing), the model can be pretty lousy.
The main issue we’ve overlooked is the transient behavior of the motor. Not only is the coil of wire an electromagnet, it’s also an inductor. Recall that the voltage across an inductor with inductance L is:
dI V = L | (16) dt

If the current is changing quickly, the inductor can develop a very large voltage! Many motor controllers support a controllable “slew rate”; this is a way of limiting the rate at which the applied voltage changes (and hopefully the current as well!) Large voltage transients are not good for circuits, and large motors can develope enormous transients on the order of tens or hundreds of volts.

### 3.4 Summary

We’ll continue to use our simple model for the rest of this article. Here’s what you need to remember:

- The Back EMF of a motor (Vemf ) is proportional to the speed of the motor.

Break-beam sensor

Clockwise rotation:

Counter-Clockwise rotation:

4

- Motor current is proportional to torque.
- We drive motors with PWM, which allows us to approximately control Vapplied.

### Deadreckoning Sensors

In order to build an odometry system, you must have a way of measuring the angular velocity of the motor. This can be accomplished in a number of ways:
- Mono Phase Encoders. A sensor is placed on the motor shaft or wheel such that when the shaft rotates, the circuitry generates alternating 1’s and 0’s. One way of implementing a simple encoder is by attaching a disc with holes to the shaft, and using a breakbeam sensor to detect when a hole passes by. A mono phase encoder can not determine the direction of motion. A serious failure mode occurs when the motor is essentially stationary with a hole halfway in front of the sensor: environmental noise can cause the encoder to trigger and untrigger, making it appear as though the shaft is rotating.

Figure 5: Simple Encoder. As a perforated disk rotates, a breakbeam sensor alternates between 1 and 0. The direction of motion is ambiguous.

- Quadrature Phase Encoders. An improvement upon mono phase encoders, quadrature phase encoders use two simple encoders arranged so that they produce waveforms 90 degrees outofphase. When the shaft rotates in one direction, signal A will “lead” signal B; when rotating in the opposite direction, signal “B” will “lead” signal A. Quadrature phase encoders are generally considered the most precise form of motor feedback, and can be quite expensive. A simple state machine can decode the quadrature phase signals into “up” and “down” pulses. The two outofphase signals provide immunity from spurious transitions due to a hole being halfway in front of one of the sensors: only one signal can be transitioning at any given time, and if this signal jumps back and forth, it maps to alternating (and cancelling) forward and backward motion.
- Tachometer. A tachometer is essentially a small motor attached to the output shaft of the main motor. It operates as a generator, where the output voltage is proportional to the angular velocity of the main motor.
- Direct Back EMF measurement. With a little extra circuitry, we can measure the back EMF of a motor directly. We set Vapplied = 0, wait for the electrical transients to die off, and then measure the voltage produced by the motor. Since we’re not applying any power to the motor, the motor will tend to slow down while we’re performing the measurement. Fortunately, it doesn’t take long for electrical transients to die off; we can measure the back EMF quickly, and then restore power.

5

Break-beam sensors
(90 degrees offset)

Clockwise rotation:

Counter-Clockwise rotation:

a

b

a

a

b

b

Figure 6: Quadrature Phase Encoder. Two simple encoders, arranged so that they pick up the same perforated holes, but 90 degrees out of phase with each other, allow the direction of rotation to be determined.

- Indirect Back EMF estimation via current sense. We can measure the amount of current flowing through the motor by putting a smallvalued resistor in the path between the motor and ground. Ohm’s law tells us that the voltage across that resistor will be proportional to the current.
If we know the motor current, the applied voltage (which we’re controlling), and the resistance of the motor winding, we can estimate the back EMF. Solving Eqn 15 for

Vemf

Vemf = Vapplied − IRwinding | (17)
- Gyro heading adjustment. Some vehicles have a gyroscope, which can provide an estimate of the vehicle’s angular rate dθ/dt. Gyros drift over time, but can be quite accurate over small periods of time. They can be used to improve dead reckoning accuracy, particularly when a poor motor feedback sensor is used (e.g., back EMF.)

### Odometry in Practice

Odometry can provide good deadreckoning over short distances, but error accumulates very rapidly. At every step, we inject error (noise) into not just x and y, but also θ. The error in θ is the killer, since every error in θ will be amplified by future iterations.
There are a number of basic noise sources.
- Sensor error. If we’re using anything other than quadrature phase encoders for our feedback, then our estimates of the dleft and dright will be noisy.
- Slippage. When the robot turns a corner, one wheel will, in general, slip a little bit. This means that even if the odometry data was perfect, the robot’s path would not recoverable from it.
- Error in estimate of dbaseline or in wheel diameters. We must measure the baseline of the robot and the scale factor relating angular rate and linear velocity (a function of the wheel diameter.) Even small errors in these constants can cause problems– typically, the odometry result will have a consistent veer in one direction or the other. In fact, often the wheels on the robot are slightly different sizes. Even small differences lead to large navigation errors with time.

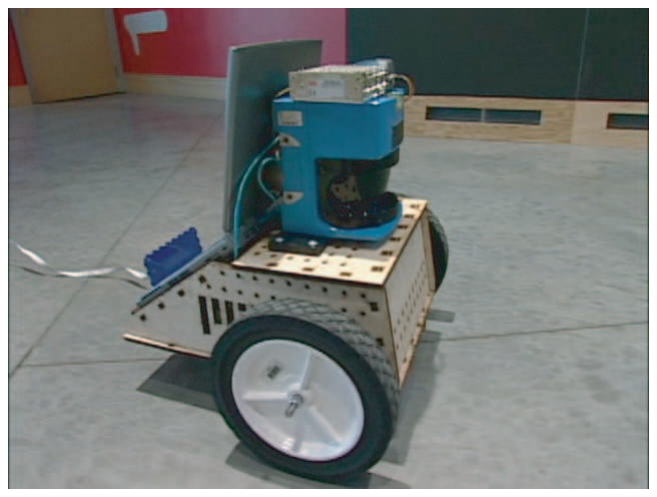
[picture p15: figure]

Figure 7: Splinter. This is the robot that collected the dataset. The vehicle, known as “Splinter”, has high quality quadrature phase encoders on each drive motor. A laptop on the back of the vehicle logged the data. The large blue device in the front of the vehicle is a laser range finder, not used in this article.

You should be itching to try out odometry now, and fortunately, there’s a dataset waiting for you! In this section, we’ll walk through a few examples in Matlab.
The dataset consists of 200 meters of odometry and gyro data from an experiment that lasted about 10 minutes. The vehicle that collected the data is shown in Fig. 7. The vehicle left the lab, travelled around a large open space in a clockwise (as viewed from the top) direction three times, then reversed direction and travelled around the same loop once in the opposite direction. Finally, it returned to lab.
A good odometry result is shown in Fig. 8. While the robot started and stopped in (approximately) the same space, notice how the odometry estimate is quite different at the beginning and end. A small error in θ causes all subsequent navigation to be rotated out of alignment.
The dataset is available from /mit/6.186/2005/doc/odomtutorial. Copy it into a directory and start matlab. The data is contained in a single array called “data”. Each row in the dataset is a set of observations made at a single point in time. A helper script, “setup.m” is provided which loads the dataset and sets up a few constants. These constants are TIME, LEFTTICKS, RIGHTTICKS, LEFTCURRENT, RIGHTCURRENT, LEFT-PWM, RIGHTPWM, and GYRO, and correspond to the column numbers in which data of different types is stored. To get started, type:

>> setup

Note that the odometry data is provided in units of ticks: the amount of forward (or backward) motion that occured since the last sample. Ticks are related to distance (and angular rate) by constant scale factors, which are characteristics of the robot’s geometry. We mentioned before that the baseline, the distance between the left and right wheels, is also a characteristic of the robot.
These measurements are made using a ruler, and are inexact. One of our tasks will be to find better values of the parameters.
Parameter | Value
baseline | 0.45 meters
metersPerTick | 0.000045 meters

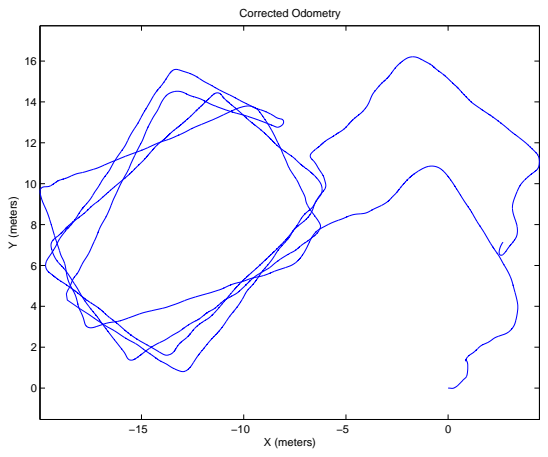
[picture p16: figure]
X (meters); Y (meters); Corrected Odometry

Figure 8: Good odometry result. This result was obtained by manually optimizing the rigid parameters of the vehicle until the path best resembled the actual trajectory. Note that the trajectory, in fact, started and ended at approximately the same position; even good odometry results can contain significant errors.

Problem 1. Examining the raw odometry data

Let’s get familiar with the data by plotting the left versus right wheel odometry ticks; we’ll be able to see how fast the left and right wheels are moving.

>> clf;
>> hold on;
>> plot(data(:,LEFTTICKS),’r’);
>> plot(data(:,RIGHTTICKS),’b’);

The command “clf” clears the figure, “hold on” allows multiple plots to be displayed on top of each other, and the two plot commands plot the vector of data in either red (’r’) or blue(’b’).
Compare the instantaneous velocity of the left and right wheels to the odometry results in Fig. 8. Identify in the velocity plot where the robot was turning.

Problem 2. Plotting the gyro data

Now let’s take a look at the gyro’s reported angular position over time. Plot the gyro data over time (the commands should look much like a previous example.) Your figure should look something like Fig. 9.
The shape of this graph is characteristic of a robot path which was mostly piecewiselinear; the robot goes straight for a while (the graph is horizontal), turns (the graph is vertical), then goes straight again.
Gyros tend to drift (a roughly uniform linear deviation over time.) We try to calibrate our gyros as carefully as we can so that the drift is small, but often our final data still contains drift. Look at the horizontal segments of the graph: they aren’t quite horizontal. Compute a better estimate of the gyro by finding a drift rate which makes the graph look more like Fig. 9.
You can do this with code like this:

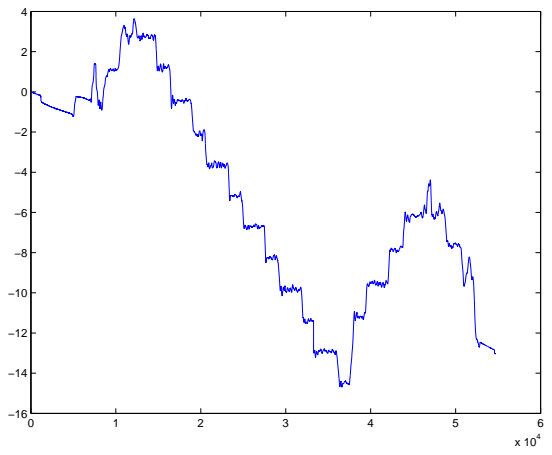
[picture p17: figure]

Figure 9: Adjusted gyro data. The robot traveled in straight line segments, punctuated by (roughly) 90 degree turns. This is readily evident from the gyro data.

>> gyro = unwrap(data(:,GYRO));
>> driftrate = <fill in this value>;
>> gyrocorrected = gyro + data(:,TIME)*driftrate;

Make sure you understand how this code works. Try it with and without the “unwrap” command. Obviously, you’ll need to experiment with different values of driftrate. Dealing with 2π wraparound is tricky, and many bugs can be introduced by neglecting it!
A fancy way of doing the calibration is to find some metric that “measures” the goodness of the drift rate. Suppose you assume that the starting orientation and end orientation were different by π/2; could you compute the correct drift rate from this?

Problem 3. Basic odometry

Your next task is to replicate the odometry result in Fig. 8. This is the most “key” problem in this whole tutorial, so don’t skip it!
Use the equations derived in this section to compute the change in θ at each time step. You can integrate this by using the cumsum command. You’ll now have a vector of the value of θ for every time step which you can use to compute the change in x and y. Using cumsum again, compute the actual x and y position. Plot the result.
Your first attempt will look like Fig. 10. These results are not terribly good, but that’s largely because the metersPerTick and baseline parameters were only estimates. Try to improve the odometry result by adjusting the parameters. Remember that metersPerTick might actually be different for the left and right wheel!
It may seem a bit tedious to optimize the parameters, and to a degree, it is. However, it is possible (and desirable) to develop an intuition for how the parameters affect the odometry result. You should be able to look at a result and say to yourself, “Hmm, I think the baseline distance is too short.”
When optimizing parameters by hand, we often use the shape of the robot path as our metric, mostly ignoring the scale. Can multiple sets of values for the baseline and metersPerTick result in the same path shape?
You should also be aware of overfitting. The more “knobs” we have to adjust the size and shape of our path, the more likely we are to be able to coax it into a shape we want–

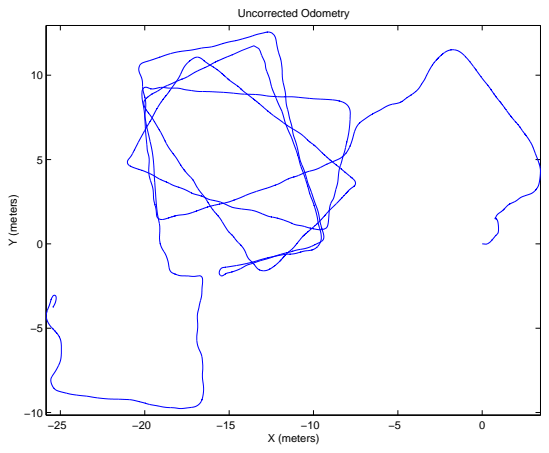
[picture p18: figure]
X (meters); Y (meters); Uncorrected Odometry

Figure 10: Uncorrected Odometry. Your first attempt at odometry should match this figure.

regardless of what the data actually tells us. Our goal is to get the best general purpose values of our parameters– ones that will be useful on future navigation missions, not get the absolute best result on a single, controlled (and perhaps contrived!) experiment. Remember that on any actual experimental run, it is much more likely that there was some error, than that there was no error.
Even with only three parameters (leftMetersPerTick, rightMetersPerTick, and baseline) it is quite possible to overfit, particularly when the dataset is relatively short. A general strategy for dealing with overfitting is to use crossvalidation: fit parameters to a subset of the data, and test it on a disjoint subset of the data. We can’t readily do that here, since we only have one relatively short dataset.

Problem 4. Gyroassisted odometry

Suppose your robot is a tricycle, with only the center wheel having an optical encoder. You no longer have dleft and dright– you only have dcenter. This means that you cannot compute changes in θ.
If you have a gyro, you could use the gyro’s estimate of heading instead! That is your challenge in this problem. Using the gyro data that you adjusted in Problem 1, recompute the odometry using only dcenter. Your graph should look similar to Fig. 11.
Is the path better or worse?
If you have dleft, dright, and gyro data, how could you fuse the two independent estimates of θ to get a better value of θ? If you’re interested in this, you should read about Kalman filters. I recommend Chapter 1 of Peter Maybeck’s book, “Stochastic Models, Estimation, and Control”; a PDF is available on the MASLab website.

Problem 5. Estimating velocity with back EMF

In the last problem, we assumed we didn’t have complete odometry data. Now we’re going to assume we don’t have any!
The dataset contains a log of the PWM values given to the motor controller, as well as the current consumption. A PWM value of -255 corresponds to about -12V, while +255 corresponds to +12V. The current consumption is given in amps, and the motor winding has a resistance of 3.5 Ohms.

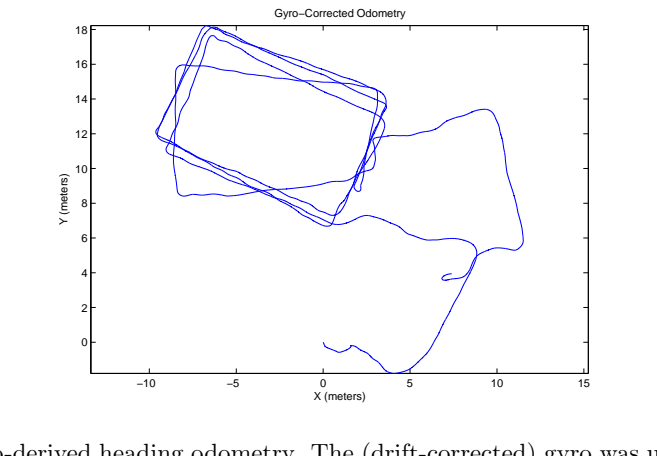
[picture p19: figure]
X (meters); Y (meters); Gyro−Corrected Odometry

Figure 11: Gyroderived heading odometry. The (driftcorrected) gyro was used exclusively for heading. You should replicate these results, and try to improve them further by fusing the odometryderived heading and the gyroderived heading.

Using Eqn. 17, estimate Vemf of the motor from these parameters. We know that Vemf is proportional to angular velocity, but what is the scale factor? We could look it up on the motor’s datasheet, but it’s probably not terribly accurate anyway.
Let’s consider a single wheel. We have it’s Vemf and its actual velocity as measured by the quadrature phase encoders. To estimate velocity, you’ll need to consider the amount of time that elapsed during every time step. You can compute this using:

>> dtime = [ 0; diff(data(:,TIME))]

One of the irritating things about working with real systems is that data doesn’t always cooperate. It’s entirely possible (in fact, likely) that you may encounter intervals in which zero time elapsed. When you compute the velocity during this interval, you must be careful to avoid a dividebyzero! A good way of dealing with this is to estimate the velocity by looking at a window spanning several time samples. This can also serve to filter out some of the noise!
We know that Vemf and velocity should be proportional to each other. Time for an upsetting fact: there’s probably some nonlinear offset as well. In other words, let’s model the system as:
velocity = x1 ∗ Vemf + x2 | (18)
We want to solve for x1 and x2, and we know the other two quantities.
This is (hopefully) true at every timestep, so let’s write this in matrix form. Let B be the matrix of actual velocities, and let A be a matrix with Vemf in the first column and 1s in the second column (in matlabeese, this is A=[vemf ones(size(vemf))]). We can then write:
Ax = B | (19)
This of course is the most basic of all Linear Algebra problems. Remember that this system is hugely overdetermined: we have thousands of simultaneous equations, and only two unknown variables. This is a good opportunity to compute a leastsquares fit. (For a reminder of the mathematics, see Strang’s 18.06 textbook, “Introduction to Linear Algebra”.)

x = (AT A)

−1AT B | (20)

We can now estimate the velocity of the motor using our coefficients x1 and x2, and compare it to our measured values using odometry. For the left wheel, you should get a graph like that in Fig. 17.

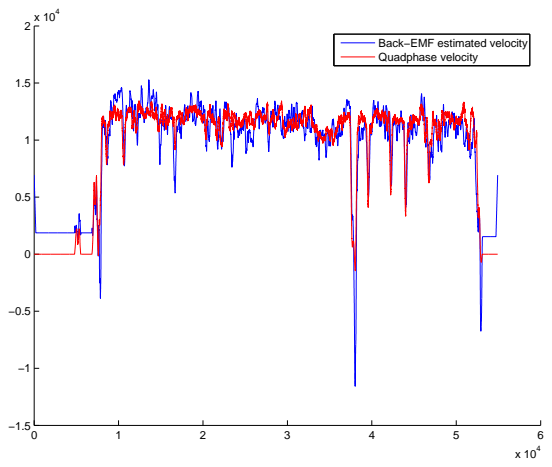
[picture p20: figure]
Back−EMF estimated velocity Quadphase velocity

Figure 12: Estimating velocity from Current Sense. Using Eqn. 17, we can estimate backemf (and thus velocity) using the motor’s current and applied voltage.

Now let’s put it all together. Estimate the velocity for the left and right wheels, and compute a trajectory without using the quadrature phase data (except for calibrating your models.)
How does it look? When does it perform well/poorly? How does it look if you use the gyro data for your θ estimate? You should be able to achieve something like Fig. 13. Keep in mind that this approach doesn’t require any optical encoders at all!

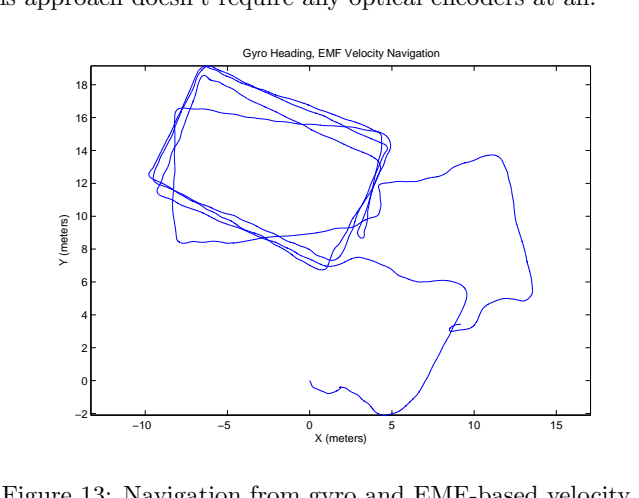
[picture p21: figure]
X (meters); Y (meters); Gyro Heading, EMF Velocity Navigation

Figure 13: Navigation from gyro and EMF-based velocity.

### 6 Conclusion

You now have a pretty good idea about what odometry is, what it can do, and what it can’t. In Maslab, you won’t have optical encoders as good as those used in this problem. But you will have a gyro, current sense, and the ability to build your own quadrature phase optical encoders.
What approaches do you think will work? Is there some other way of navigating? Maslab robots have cameras. If you pick out a feature and follow it around, can you use that to compute changes in robot orientation? If you find a feature of known size, can you estimate how far away you are?
You can purchase other sensors too– perhaps an electronic compass. Inexpensive electronic compasses might be low resolution, but they won’t drift like a gyro. Can an electronic compass plus a gyro be a powerful navigation aid?

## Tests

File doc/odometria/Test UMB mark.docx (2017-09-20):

Test UMB mark

Sono fatti su piano con piastrelle.

I comandi sono inviati da BT. Quando lo stato passa a 0 viene dato il comando successivo. A seconda di quando viene ricevuto si possono avere viaggi diversi.

Modficato fw per avere uno stato diverso da zero durante la rampa di fermata.

Ripeto le prove con i valori nominali.

#define GIRO_RUOTA 2.728
#define GIRO_RUOTA_DX 2.728
#define GIRO_RUOTA_SX 2.728

Rispetto le coordiante di ARI02

y

^
|
|
|
|------------------------------------ > y

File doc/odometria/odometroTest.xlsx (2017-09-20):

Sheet: odometroTxt
 |  |  |  |  |  |  |  | 5.25 | giorRuota
 |  |  |  |  |  |  |  | 150 | baseLine
1000 | 908 |  |  |  |  |  |  |  |  | 0.00 |  | 0.00 | 360
dDxCnt | dSxCnt |  | deltaC | teta | xpos | ypos | dteta | deltaCcalc | sumC | teta_k |  | teta_sum
0 | 0 | 0 | 0.00 | 0.00 | 0.00 | 0.00 |  | 0.00 | 0.00 | 0.00 | 0.00 | 0.00 | 360
0 | 0 | 0 | 0.00 | 0.00 | 0.00 | 0.00 | 0.00 | 0.00 | 0.00 | 0.00 | 0.00 | 6.28 | 0
0 | 0 | 0 | 0.00 | 0.00 | 0.00 | 0.00 | 0.00 | 0.00 | 0.00 | 0.00 | 0.00 | 6.28 | 0
0 | 0 | 0 | 0.00 | 0.00 | 0.00 | 0.00 | 0.00 | 0.00 | 0.00 | 0.00 | 0.00 | 6.28 | 0
0 | 0 | 0 | 0.00 | 0.00 | 0.00 | 0.00 | 0.00 | 0.00 | 0.00 | 0.00 | 0.00 | 6.28 | 0
2 | 0 | 5.25 | 0.07 | 5.24 | 0.37 | 0.00 | 5.24 | 10.50 | 10.50 | 0.07 | 4.01 | 6.35 | -4.012738854
3 | 3 | 15.75 | 0.07 | 20.95 | 1.48 | -0.07 | 15.71 | 31.50 | 42.00 | 0.00 | 0.00 | 6.35 | -4.012738854
5 | 5 | 26.25 | 0.07 | 47.13 | 3.34 | -0.07 | 26.18 | 52.50 | 94.50 | 0.00 | 0.00 | 6.35 | -4.012738854
6 | 6 | 31.5 | 0.07 | 78.55 | 5.60 | -0.07 | 31.42 | 63.00 | 157.50 | 0.00 | 0.00 | 6.35 | -4.012738854
6 | 7 | 34.13 | 0.04 | 112.65 | 6.89 | -0.07 | 34.10 | 68.25 | 225.75 | -0.04 | -2.01 | 6.32 | -2.006369427
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

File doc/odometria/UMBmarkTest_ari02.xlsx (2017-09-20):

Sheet: test2
compensazione errori sitematici con test quadrilatero bidirezionale |  |  |  |  |  |  |  | 2017-08-14
UMBmark —
A Method for Measuring, Comparing, and Correcting
Dead-reckoning Errors in Mobile Robots |  |  |  |  |  |  |  | diametri ai valori nominali: |  |  | 2.7280
 | L | 2.4 | m |  |  |  |  |  |  | baseline attuale |  | 0.13
risultati test
test cw | x fisico | y fisico | x arianna | y arianna |  | ex | ey | r
1 | 0.91 | 0.035 | 0.0287 | -0.071 | -4.78 | 0.8813 | 0.106 | 0.888 |  |  | beta | 0.1208802083
2 | 0.33 | 0.115 | 0.04 | -0.058 | -4.74 | 0.29 | 0.173 | 0.338 |  |  | R | 19.86646001
3 | 0.855 | 0.21 | 0.043 | -0.066 | -4.83 | 0.812 | 0.276 | 0.858 |  |  | Ed | 1.006565172 |  | 69.46794956 | Ddx | 69.24066112 | 2.719074404
4 | 0.77 | 0.14 | 0.035 | -0.07 | -4.95 | 0.735 | 0.21 | 0.764 |  |  |  |  |  | 69.46794956 | Dsx | 69.695238 | 2.736925596
5 | 1.29 | 0.315 | 0.045 | -0.088 | -4.57 | 1.245 | 0.403 | 1.309 |  |  |  |  |  | 69.46794956 |  | 69.46794956 | 2.728
 | 0.105 | 0.575 | 0.072 | -0.049 |  | 0.033 | 0.624 | 1.309 | rcw max |  | alfa | -0.1208802083 | -6.925925764
 |  |  |  |  | xcg cw | 0.66605 |  |  |  |  | Eb | 0.9986586881 |  | 69.46794956
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

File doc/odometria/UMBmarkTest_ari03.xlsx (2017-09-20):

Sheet: test2
compensazione errori sitematici con test quadrilatero bidirezionale |  |  |  |  |  |  |  | 2017-08-14
UMBmark —
A Method for Measuring, Comparing, and Correcting
Dead-reckoning Errors in Mobile Robots |  |  |  |  |  |  |  | diametri ai valori nominali: |  |  | 2.7280
 | L | 2 | m |  |  |  |  |  |  | baseline attuale |  | 0.138
risultati test
test cw | x fisico | y fisico | x arianna | y arianna |  | ex | ey | r |  |  |  | su x | su y
1 | 1.49 | -1.15 | 0.0023 | -0.047 | -4.82 | 1.4877 | -1.103 | 1.852 |  |  | beta | 0.1193479167 | -0.4009625
2 | 1.57 | -0.9 | -0.01 | -0.034 | -4.75 | 1.58 | -0.866 | 1.802 |  |  | R | 16.76767842 | -5.02156852
3 | 1.61 | -0.99 | 0.039 | -0.016 | -4.7 | 1.571 | -0.974 | 1.848 |  |  | Ed | 1.008264127 | 0.9728910436 | 1.131 | Ddx | 1.126345867 | 1.146540762
4 | 1.66 | -1.18 | 0.056 | -0.02 | -4.8 | 1.604 | -1.16 | 1.979 |  |  |  |  |  | 1.131 | Dsx | 1.135654133 | 1.115459238
5 | 1.75 | -1.13 | 0.032 | -0.04 | -4.64 | 1.718 | -1.09 | 2.035 |  |  |  |  |  | 69.46794956 |  | 69.46794956 | 2.728
 |  |  |  |  |  | 0 | 0 | 2.035 | rcw max |  | alfa | -0.1193479167 | 0.4009625
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

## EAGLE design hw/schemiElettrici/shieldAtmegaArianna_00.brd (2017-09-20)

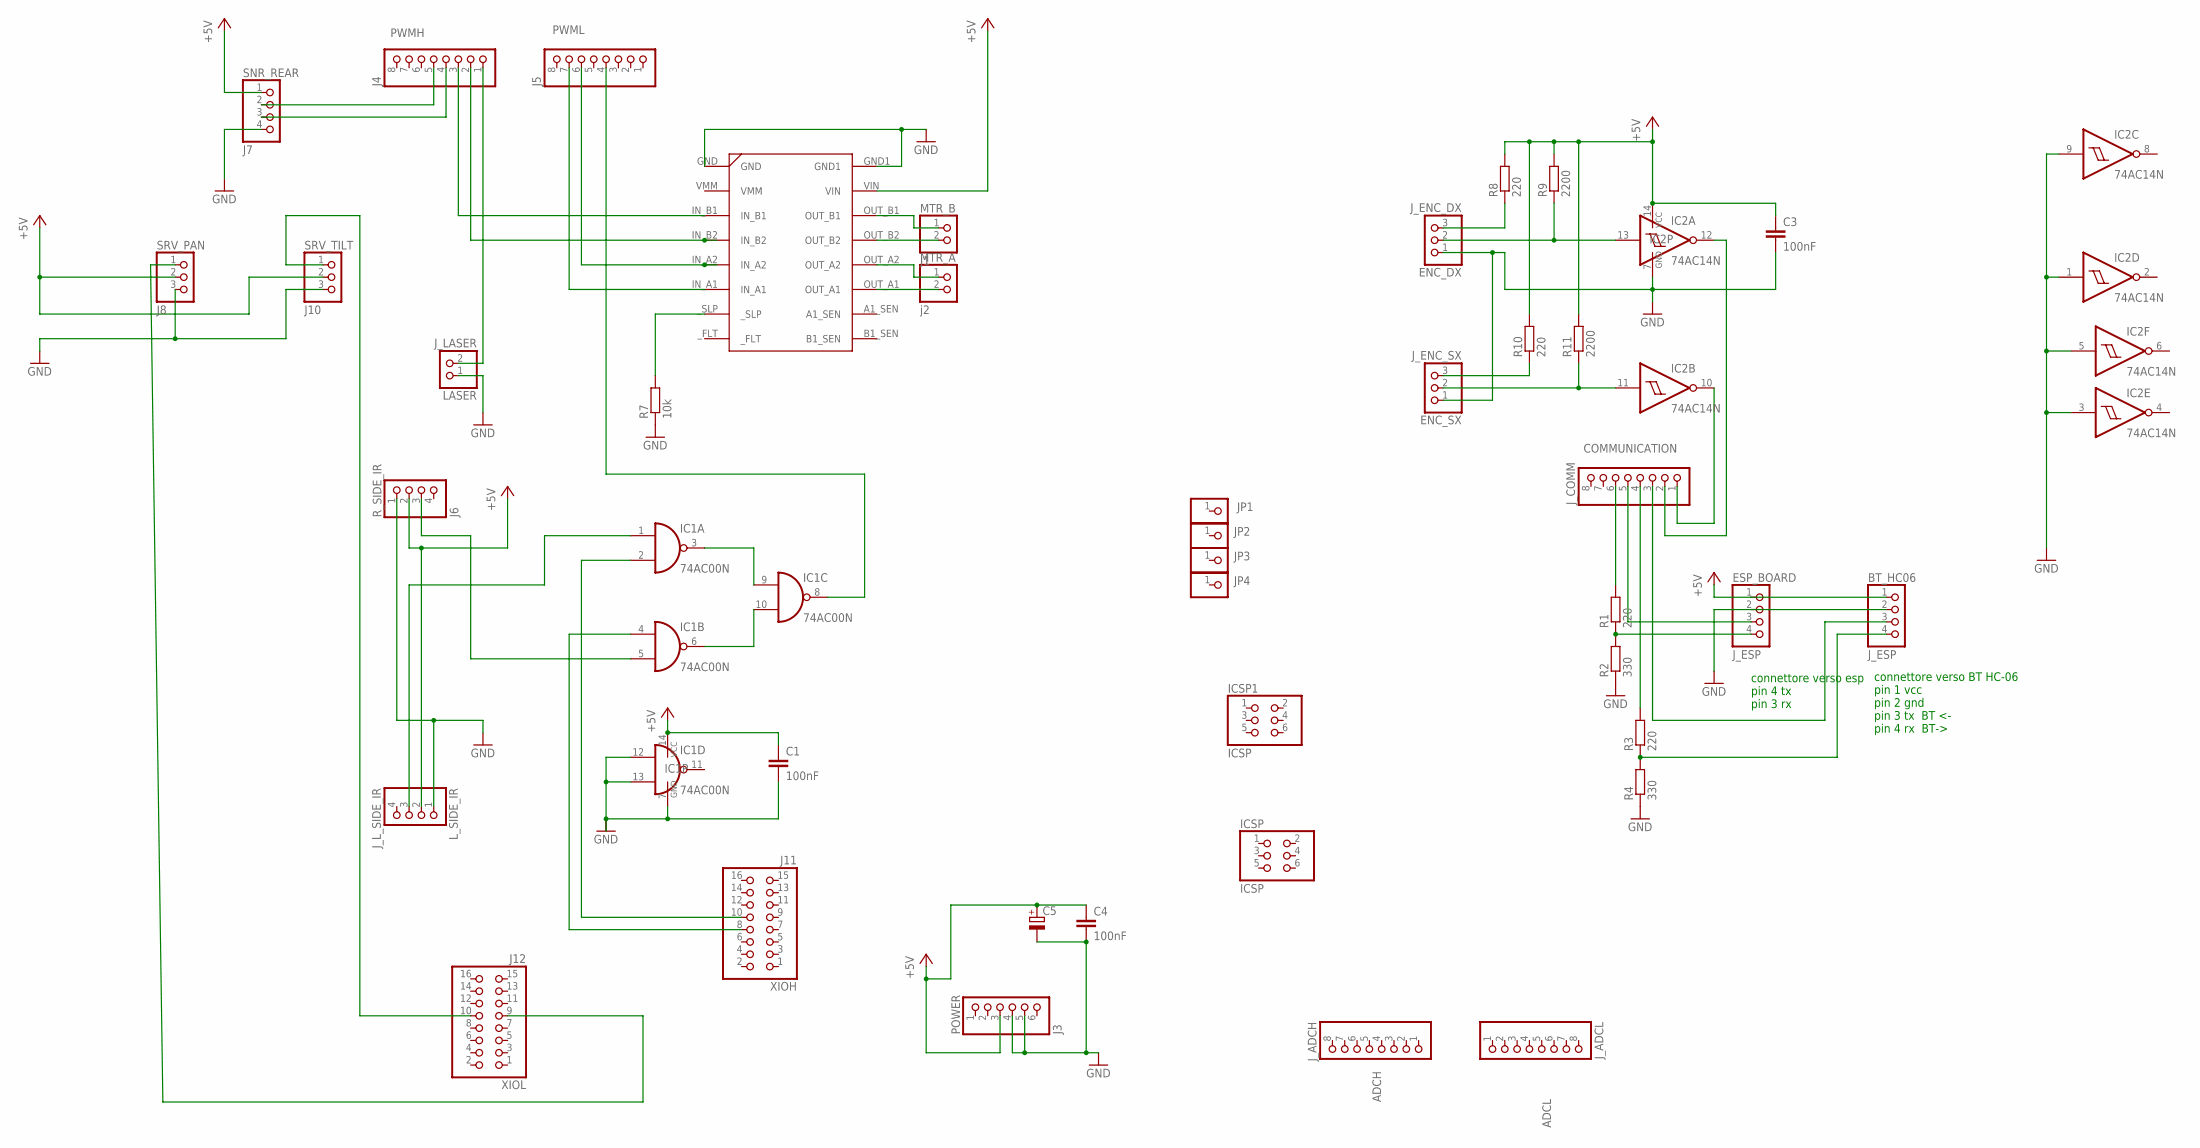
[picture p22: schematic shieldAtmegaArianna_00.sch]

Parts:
ADCH: J_ADCH; 1X08
ADCL: J_ADCL; 1X08
BT_HC06: J_ESP; 1X04
C1, C3, C4: 100nF; C050-025X075
C5: CPOL-EUE5-8.5; E5-8,5
COMMUNICATION: J_COMM; 1X08
ENC_DX: J_ENC_DX; 1X03
ENC_SX: J_ENC_SX; 1X03
ESP_BOARD: J_ESP; 1X04
IC1: 74AC00N; DIL14
IC2: 74AC14N; DIL14
ICSP, ICSP1: ICSP; 2X03
JP1, JP2, JP3, JP4: PINHD-1X1; 1X01
LASER: J_LASER; 1X02
L_SIDE_IR: J_L_SIDE_IR; 1X04
MTR_A: j2; 1X02
MTR_B: J1; 1X02
POWER: J3; 1X06
PWMH: J4; 1X08
PWML: J5; 1X08
R1, R3, R8, R10: 220; 0207/10
R2, R4: 330; 0207/10
R7: 10k; 0207/10
R9, R11: 2200; 0207/10
R_SIDE_IR: J6; 1X04
SNR_REAR: J7; 1X04
SRV_PAN: J8; 1X03
SRV_TILT: J10; 1X03
U$1: DRV8803; 8X5CARRIER
XIOH: J11; 2X08
XIOL: J12; 2X08

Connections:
+5V: BT_HC06.1, C1.1, C3.1, C4.1, C5.+, ESP_BOARD.1, IC1.14 (VCC), IC2.14 (VCC), L_SIDE_IR.2, POWER.3, R8.2, R9.2, R10.2, R11.2, R_SIDE_IR.2, SNR_REAR.1, SRV_PAN.2, SRV_TILT.2, U$1.VIN
ECHO: PWMH.4, SNR_REAR.3
GND: BT_HC06.2, C1.2, C3.2, C4.2, C5.-, ENC_DX.1, ENC_SX.1, ESP_BOARD.2, IC1.7 (GND), IC1.12 (I0), IC1.13 (I1), IC2.1 (I), IC2.3 (I), IC2.5 (I), IC2.7 (GND), IC2.9 (I), LASER.1, L_SIDE_IR.1, POWER.4, POWER.5, R2.1, R4.1, R7.1, R_SIDE_IR.1, SNR_REAR.4, SRV_PAN.3, SRV_TILT.3, U$1.GND, U$1.GND1
unnamed: MTR_B.1, U$1.OUT_B1
unnamed: MTR_B.2, U$1.OUT_B2
unnamed: MTR_A.1, U$1.OUT_A2
unnamed: SRV_TILT.1, XIOL.10
unnamed: SRV_PAN.1, XIOL.9
unnamed: MTR_A.2, U$1.OUT_A1
unnamed: PWML.7, U$1.IN_A1
unnamed: PWML.6, U$1.IN_A2
unnamed: PWMH.2, U$1.IN_B2
unnamed: PWMH.3, U$1.IN_B1
unnamed: ESP_BOARD.4, R1.1, R2.2
unnamed: BT_HC06.4, R3.1, R4.2
unnamed: COMMUNICATION.6, R1.2
unnamed: COMMUNICATION.4, R3.2
unnamed: COMMUNICATION.5, ESP_BOARD.3
unnamed: BT_HC06.3, COMMUNICATION.3
unnamed: IC1.3 (O), IC1.9 (I0)
unnamed: IC1.6 (O), IC1.10 (I1)
unnamed: LASER.2, PWMH.1
unnamed: IC1.2 (I1), XIOH.10
unnamed: IC1.5 (I1), R_SIDE_IR.3
unnamed: IC1.8 (O), PWML.4
unnamed: IC1.1 (I0), L_SIDE_IR.3
unnamed: IC1.4 (I0), XIOH.8
unnamed: R7.2, U$1._SLP
unnamed: ENC_DX.3, R8.1
unnamed: ENC_DX.2, IC2.13 (I), R9.1
unnamed: ENC_SX.3, R10.1
unnamed: PWMH.5, SNR_REAR.2
unnamed: ENC_SX.2, IC2.11 (I), R11.1
unnamed: COMMUNICATION.2, IC2.12 (O)
unnamed: COMMUNICATION.1, IC2.10 (O)

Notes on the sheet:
connettore verso esp pin 4 tx pin 3 rx
connettore verso BT HC-06 pin 1 vcc pin 2 gnd pin 3 tx BT <- pin 4 rx BT->

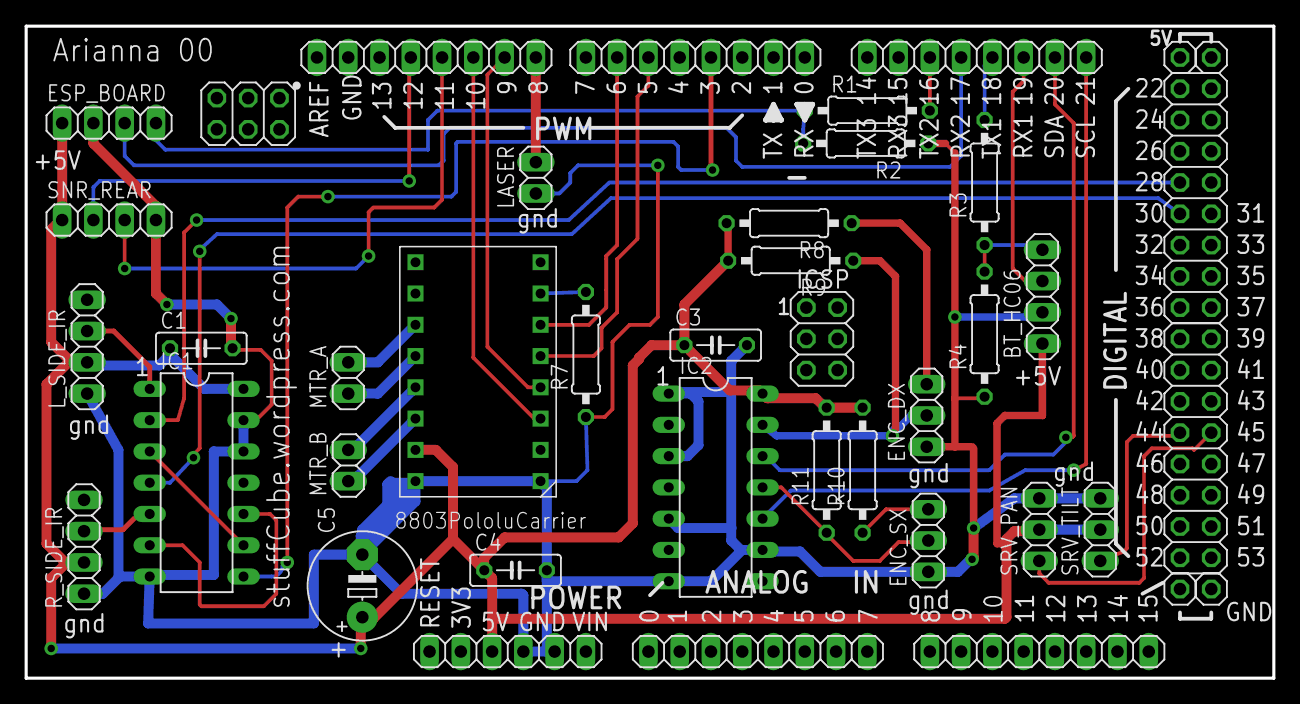
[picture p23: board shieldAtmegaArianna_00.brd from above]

Board: 2 copper layers, 101.3 x 53.0 mm, 42 parts (0 on the bottom side), 35 nets.

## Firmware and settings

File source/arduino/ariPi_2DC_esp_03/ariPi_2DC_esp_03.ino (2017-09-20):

/*
note : 30lug16
fare un doppio movimento per la posizione
il primo fa in grosso e nel caso eccede.
il secondo si posiziona fine.
la macchina a stati è già pronta

giocare con baseline per la giusta larghezza

R5 si ferma troppo avanti, l'angolo che trova è sbagliato
devo dare due R5 per farlo andare


testare con modifica VA_zero attiva, nei test precedenti non lo era
testare modo R5 che gira su una ruota.


sistemata cablatura:
motore DX morsetti A - per il piu e meno fare foto
motore SX morsetti B
IR DX a ingDX
IR SX a ingSX
Encoder SX a ing SX
Encoder DX a ing DX

parametri taratura salvati e recuperati da E2prom
talvolta perde dei dati (giroRuota). Confusione con aggancio BT ??
messo comando f per leggere distanza degli IR
R5 e R6 girano ma non danno risultati ripetibili
m sonar rivedere

 



aggiustare le dirVx = 0 gestite in odometro


*/
/*
 * arianna
 * giorgio323@gmail.com
 * infostuffcube@gmail.com
 * 
 * 16nov16	inizio
 
	test su sensore ir
	l'idea è trovare il tempo a 1 rispetto al tempo totale
	questo è un indicatore della distanza
	
	10dic16	sensore rotazione motore (odometro)	
			spostato su Raspberry la compilazione
			ID_000  digitalPinToInterrupt(SIDE_IR_PIN) non dichiarato

	27dic16	comandi da seriale
			gestione arrivo in posizione 
			aggiunto sonar montato su servo
			
			per trovare la direzione da puntare cerco il punto a distanza minima
			con un algoritmo di bisezione
			faccio con uno script esterno
 
	02gen17	penso a gestire sensore dx e sx
	numbers 0 (on digital pin 2) and 1 (on digital pin 3)
	
	19gen17	differenziale elettronico
			tolgo ovfTimer perchè usato dai PWM
			gestire misura sensore senza interrupt timer

	28gen17	add blueTooth on serial port1
			vanno ignorati i vari messaggi da BT
			quando non è connesso
			code 0000
			http://wiki.seeedstudio.com/wiki/Bluetooth_Bee
			
	23mar17 ID_001 rimosso limite angolo teta		

	14mag17 si aggiunge comunicazione con esp ID_002
			si usa la serial2 verso esp
			modifica protocollo Alessandro Airaghi
			
	21mag17 ripristinato BT in parallelo ID_003
			Ok

	07giu17 cambiati encoder
			# come indicatore inizio msg monitor
			  aggiunto comado di home 'H', prende la posizione attuale come 0, 0, 0
			cambiato terminatore seriale, da println a print + \n ID_004
			nel controllo di teta porto -2 <= S <= 2  ID_005

	29lug17	macchina a stati e rampa su tetaRef Rr
			
			
	11ago17	comando H modificato (distanza, odometro, lastPosition = 0.0)		
			introdotto statoRun 99. Questo indica una rampa in corso.
			precedentemente lo statoRun 0 era presente anche durante la rampa di fermata
			il 99 serve per eviatre di inserire un ritardo coi comandi seriali per attendere la fine rampa
			
			nella lettura encoder se tensione al motore zero non conto impulsi.
			serve per evitare che quando curva su una ruota ferma possano esserci movimenti
	
	22ago17	ariPi_2DC_esp_02.ino
			messo ordine su nomi e posizioni encoder motori etc
			sistemati segni delle reazioni
			questo per capire su cosa si agisce
			Lettura velocità angolare e lineare

	10set17	diventa _03
			salvo dati di taratura in eeprom	ID_006
			rivisti sensori IR left e dx
			
 * Simple test for the DRV8833 library.
 * The DRV8833 is a dual motor driver carrier made by Pololu.
 * You can find it here: https://www.pololu.com/product/2130

 */



#include <SPI.h>
#include <SD.h>
#include <Servo.h> 
#include <TimerOne.h>
#include <EEPROM.h>			// ID_006
// #include <NewPing.h> usa interrupt timer2

//#define ARI2  1
//#define ARI3  1

#define SCRIVI 	0
#define LEGGI 	1
#define DEFAULT 2

#define	DUE_PI	6.28318

//Servo sterzo;          	// create servo object to control a servo 
Servo servoPan;      	// create servo object to control a servo 
Servo servoTilt;      	// create servo object to control a servo 

#define TRIGGER_PIN	11
#define ECHO_PIN	  12		// FILO BIANCO BLU



//********** ID_002
//seriale di comunicazione con esp uso pin 7 e 9 
//SoftwareSerial ESPserial(7, 9); // RX | TX
#define ESPserial Serial2

String inputString 		= "";
String inputStringTmp 	= "";
int okcomm				= 0;
static String risposta;
char port	= 0;

//**********fine ID_002

  
//NewPing sonar(TRIGGER_PIN, ECHO_PIN , 200); // usa intTimer2 conflitto

// dc motor
#include <DRV8833.h>

// Create an instance of the DRV8833:
DRV8833 driver = DRV8833();

// Pin numbers. Replace with your own!
// Attach the Arduino's pin numbers below to the
// Ain1 and Ain2 DRV8833 pins.
// N.B. la libreria sembra non gestire i pin 44-46 (timer diverso) 
const int MTR_A_DX_P1 	= 5;
const int MTR_A_DX_P2 	= 6;
const int MTR_B_SX_P1 	= 9;
const int MTR_B_SX_P2 	= 10;


int motorSpeedRef 	= 0;
int state 			= 0;
int direzione 		= 1;
int dirVA			= 1;		// ID_005
int dirVB			= 1;

int	VB_zero			= 0;
int VA_zero			= 0;


// #define SERVO_PIN   		9    	// Digital IO pin connected to the servo pin.
#define SERVO_PAN_PIN  		45    	// Digital IO pin connected to the servo pin.
#define SERVO_TILT_PIN  	44    	// Digital IO pin connected to the servo pin.

#define SIDE_IR_PIN			3		// sensore IR 
#define GIRO_DX_PIN			20		// sensore su rotazione albero motore
#define GIRO_SX_PIN			21		// sensore su rotazione albero motore

#define R_SIDE_FRONT		30		// seleziona sensore frontale Dx
#define L_SIDE_FRONT		28		// sensore frontale Sx

	

#define ledPin 				13
#define laserPin 			8
#define tensionePin 		A4
#define	BT_CONNECTION_PIN	51

#define  TEST_MOTORE    	0
#define  TEST_STERZO    	1
#define  TEST_SENSORS   	2
#define  TEST_CONTROLLO 	3
#define  TEST_GIRO_SENSOR 	4


int sideIRstate 	= 0;
int sideIRcnt 		= 0;
int frontIRstate 	= 0;
int measureAvailable = 0;
unsigned long totTimeAtOne;
unsigned long measuringTime;
int startMeasureIRSide  = 0;

long odometroCnt, odometroDxCnt, odometroSxCnt;
char BTstate;	

float 	percentoUno;
float 	x;
int 	i;

char firstRun;
float lastPosition;

// tempo del controllo sterzo, posizione etc in ms
#define TEMPO_CONTROLLO 100

/*	V = w*r	-> w=V/raggio di curvatura
	a larghezza tra due ruote
	V1 = V*(r+a/2)/r = V(1 + a/2r)
	
*/


#define S_NEUTRO_FWD		0.0//ari02-0.05	// con questo valore va crica diritto
#define S_NEUTRO_REV		0.0//ari02-0.02	// con questo valore va crica diritto

#ifdef ARI2 
  // arianna 2 ruota sx 70 diametro
  //           ruota dx 69 diametro
  // encoder 20 ppr
  #define GIRO_RUOTA        2.728  	//  20ppr 5.25 // mm per impulso*0.5 = sviluppo ruota[mm]/ppr (pulsi per rivoluzione)
  #define GIRO_RUOTA_DX     2.719074  // 2.7083 //  20ppr 5.25 
  #define GIRO_RUOTA_SX     2.736926	//2.7275 //  20ppr 5.25 
  #define MIN_TIME_TRA_PULSE    18 	// tempo minimo tra impulsi encoder per evitare errate letture
  
  #define BASELINE 		  129.826 //150.0	// carreggiata
  #define LAGHEZZA_A_MEZZI	0.065 //0.09	// mezza carreggiata (larghezza delle due ruote)
#endif

#ifdef ARI3
  // arianna 3 ruota 47 diametro
  // encoder 35 ppr
  #define ED 0.95 //0.972891
  #define GIRO_RUOTA 			1.131 		// mm per impulso*0.5 = sviluppo ruota[mm]/ppr (pulsi per rivoluzione)
  #define GIRO_RUOTA_SX       GIRO_RUOTA*2.0/(1.0+ED) 
  #define GIRO_RUOTA_DX       GIRO_RUOTA*2.0/(1.0+1.0/ED) 
  //#define GIRO_RUOTA_SX       1.1465408 
  //#define GIRO_RUOTA_DX       1.1154592
  #define MIN_TIME_TRA_PULSE    9  		// unsigned long  20 ppr 18 // tempo minimo tra impulsi encoder per evitare errate letture
  
  #define BASELINE 		  	137.817 		// carreggiata
  #define LAGHEZZA_A_MEZZI	0.069 		// mezza carregiata (larghezza delle due ruote)
#endif

float ED 			= 1.0;
float ED_BASE 		= 1.0;
float GIRO_RUOTA 	= 1.0;
float BASELINE 		= 130.0;

float GIRO_RUOTA_SX = 1.0;
float GIRO_RUOTA_DX = 1.0;
float LAGHEZZA_A_MEZZI = 0.065;
unsigned long MIN_TIME_TRA_PULSE = 9;  		// unsigned long  20 ppr 18 // tempo minimo tra impulsi encoder per evitare errate letture


// aggiorno per encoder da 35 ppr prima erano 20 
/*
ari 1 con encoder da 20 ppr
#define GIRO_RUOTA        2.625 //  20ppr 5.25 // mm per impulso*0.5 = sviluppo ruota[mm]/ppr (pulsi per rivoluzione)
#define GIRO_RUOTA_DX     2.625 //  20ppr 5.25 
#define GIRO_RUOTA_SX     2.615 //  20ppr 5.25 
#define MIN_TIME_TRA_PULSE    9 //  20 ppr 18 // tempo minimo tra impulsi encoder per evitare errate letture
*/
/*
ari 1 con encoder da 35 ppr
#define GIRO_RUOTA        1.5     //  35ppr // mm per impulso*0.5 = sviluppo ruota[mm]/ppr (pulsi per rivoluzione)
#define GIRO_RUOTA_DX     1.5     //  35ppr 
#define GIRO_RUOTA_SX     1.494   //  35ppr 
#define MIN_TIME_TRA_PULSE   5    //  35ppr tempo minimo tra impulsi encoder per evitare errate letture
*/


#define E_POSIZIONAMENTO  	10
#define E_APPROCCIO			300

/*
	MODERATA 		è il pwm di movimento normale
	APPROCCIO 		durante l'avvicinamento alla poszione
	ACCELERAZIONE 	nella fase del partenza
*/
#define FERMO			0	
#define MODERATA		190
#define APPROCCIO		110
#define ACCELERAZIONE	160
#define AVANTI			0
#define INDIETRO 		1

#define KP_DEF			8

#define MAX_STERZO	1.0

// parametri lettura e/o scrittura
int 	statoRun 		= 0;
float 	odometro 		= 0;
float 	distanza 		= 0;
float 	raggiorSterzo	= 0.0;
float 	errore;
int		viaLibera 		= 0;
int 	motorSpeed 		= 0;
int 	motorSpeedValue = MODERATA;
int 	panAngle 		= 90;
int 	tiltAngle 		= 90;
char 	laser 			= 0;
int 	misura;
float	kp 				= KP_DEF;		// k proporzionale
float	kpTeta			= 2.0;			// k proporzionale per teta
float	kiTeta			= 0.02;			// k i per teta

float 	MAX_S			= 0.2;			// max_s = LARGHEZZA_A_MEZZI/Raggio massimo 
float 	teta 			= 0.0;					// teta attuale
float 	xpos, ypos 		= 0.0;
float 	tetaRef			= 0.0;
// temporaneo

float 	VA, VB;
int 	cntStop = 0;
int 	mode = TEST_STERZO;
char 	debugBT, monitorDati = 0;
float 	i_part = 0;
float 	delta_teta;
float 	deltaS;
long 	spdDxCnt, spdSxCnt;
  
void _sendBlueToothCommand(char command[])
{
    Serial1.print(command);
}
/*
 * setup BT connection
 */ 
void setupBlueToothConnection(){

String str;

    Serial1.begin(38400);                           // Set BluetoothBee BaudRate to default baud rate 38400
    Serial1.print("\r\n+STWMOD=0\r\n");             // set the bluetooth work in slave mode
    Serial1.print("\r\n+STNA=SeeedBTLamp\r\n");    	// set the bluetooth name as "SeeedBTSlave"
    Serial1.print("\r\n+STOAUT=1\r\n");             // Permit Paired device to connect me
    Serial1.print("\r\n+STAUTO=0\r\n");             // Auto-connection should be forbidden here
    delay(2000);                                            // This delay is required.
    Serial1.print("\r\n+INQ=1\r\n");                // make the slave bluetooth inquirable
    Serial.println("The slave bluetooth is inquirable!");
    delay(2000);                                            // This delay is required.
	
	Serial1.setTimeout(2000);
    Serial1.flush();
	
	Serial.println("init BT done!");
}	 
	 
void setup() {
    // initialize serial:
    Serial.begin 	( 9600);
    Serial1.begin	(38400);
    ESPserial.begin ( 9600);  // ID_002
    
    Serial.println("Init: ari2DC_esp.ino da PI 13ago17");
    Serial.print  ("BASELINE: ");
    Serial.println( BASELINE   );
    Serial.print  ("GIRO_RUOTA: ");
    Serial.println( GIRO_RUOTA   );
    Serial.print  ("GIRO_RUOTA_DX: ");
    Serial.println( GIRO_RUOTA_DX   );
    Serial.print  ("GIRO_RUOTA_SX: ");
    Serial.println( GIRO_RUOTA_SX   );
	
	pinMode(ledPin, 	OUTPUT);
	pinMode(laserPin, 	OUTPUT);

	pinMode(BT_CONNECTION_PIN,  INPUT_PULLUP);
	
	pinMode(ECHO_PIN, 	INPUT);
	pinMode(TRIGGER_PIN,OUTPUT);

	// setup digital inputs for IR sensors
	pinMode(R_SIDE_FRONT, 		OUTPUT);
	pinMode(L_SIDE_FRONT, 		OUTPUT);
	pinMode(SIDE_IR_PIN, 			INPUT);
	pinMode(GIRO_DX_PIN,  		INPUT);
	pinMode(GIRO_SX_PIN,  		INPUT);

	
	digitalWrite(laserPin, LOW);

	// attaches the servo on pin .. to the servo object
	// sterzo.attach	 (SERVO_PIN);  		
	servoPan.attach  (SERVO_PAN_PIN );
	servoTilt.attach (SERVO_TILT_PIN);
	
	servoPan.write ( 90);
	servoTilt.write( 90);

	
	// Attach motors to the input pins:
	driver.attachMotorA(MTR_A_DX_P1, MTR_A_DX_P2);
	driver.attachMotorB(MTR_B_SX_P1, MTR_B_SX_P2);

	differenziale(0);
	
	
/* tolto t2_ovf in it	
// timer1 usato per servo	
//	Timer1.initialize(5000);         	// initialize timer1, and set a 5ms period
//	Timer1.attachInterrupt(IRSensors);  // attaches callback() as a timer overflow interrupt

// https://oscarliang.com/arduino-timer-and-interrupt-tutorial/
#define BIT(x) (0x01 << (x))

 	noInterrupts();           // disable all interrupts

	// Use Timer2 with 1 ms interrupts
	// OC2A & OC2B disconnected, mode 2 (CTC, Clear Timer on Compare match)
	TCCR2A = BIT(WGM21);
	// Don't force output compare (FOCA & FOCB), mode 2, Clock Select clk/128 (CS = 5)
	TCCR2B = BIT(CS22) | BIT(CS20);
	//  TCCR2A = BIT(WGM21);
	//  TCCR2B = 0;
	//  TCNT2  = 0;

	OCR2A = 125-1;            // compare match register 16MHz/256/2Hz
	//  TCCR2B |= (1 << WGM12);   // CTC mode
	//  TCCR2B |= (1 << CS12);    // 256 prescaler 
	TIMSK2 |= (1 << OCIE2A);  // enable timer compare interrupt
	
	interrupts();             // enable all interrupts
tolto t2 ovf end */ 
	
	attachInterrupt(digitalPinToInterrupt(SIDE_IR_PIN), cntSideSensor, CHANGE);
        // pin 3 interrupt 1 atMega
//	attachInterrupt(2, cntSideSensor, CHANGE);

	// odometro 
	// pin 21 (atMega) int 2	
	attachInterrupt(digitalPinToInterrupt(GIRO_DX_PIN), odometroDxMisuraHW, CHANGE);
	// pin 20 (atMega) int 3	
	attachInterrupt(digitalPinToInterrupt(GIRO_SX_PIN), odometroSxMisuraHW, CHANGE);

	/*
	il BT intasa la seriale !!!
	Status instruction port PIO1: low-disconnected, high-connected
	*/
//	if (BTstate != digitalRead(BT_CONNECTION_PIN)){


    delay(1000);

    setupBlueToothConnection();


	// ID_002 gestire BT e Wifi
 
	while (!digitalRead(BT_CONNECTION_PIN)){
		;
	}
 
	BTstate = 1;
		Serial.print("BT connection: ");
		Serial.println(digitalRead(BT_CONNECTION_PIN));
	delay (2000);
//	BTstate = digitalRead(BT_CONNECTION_PIN);


  
	Serial.flush();
	Serial1.flush();
	ESPserial.flush();  // ID_002
	
	
	DataEEprom(1);  	// carica coefficienti da e2prom
	
	
	firstRun = 1;
    Serial.println("setup done!");
    Serial1.println("setup done!");

    
}

unsigned long lastTime, lastTimeFast;
float	teta_;
float actualTetaRef;
char SM_R5 = 0;
unsigned long inizioStabilita; //Timer
float dLaterale;


void loop() {

	mode = TEST_CONTROLLO;
//	mode = TEST_MOTORE;
	
	BTstate = digitalRead(BT_CONNECTION_PIN);
	
	// ID_002
	getCmd(); // ID_003
	
	getCmd2();
	rSeriale();
	

//    odometroMisura();			
	servoPan.write ( panAngle);
	servoTilt.write(tiltAngle);

	
    if (mode == TEST_CONTROLLO){

		if (firstRun){
			Serial.println("start TEST_CONTROLLO mode");
			Serial.println("controlloAttivo");
			Serial1.println("controlloAttivo");
			raggiorSterzo = 0.0;
			servoPan.write(panAngle);
			servoTilt.write(tiltAngle);
			kp = KP_DEF;
			digitalWrite( R_SIDE_FRONT,  LOW);
			digitalWrite( L_SIDE_FRONT, HIGH);
			firstRun = 0;
		}
	
		/* statoRun
		
			0: fermo
			1: controllo sterzo da sensore dx e distanza automatico
			1: controllo sterzo da sensore dx e distanza automatico
			2: controllo distanza, strzo da parametro
			4: controllo distanza, sterzo da parametro da tetaRef vs teta odometria
			5: rotazione su se stessa
		*/
			
			// parte a 100 ms
			if ((millis()-lastTime) > 25){//TEMPO_CONTROLLO){
//				Serial.println(millis()-lastTime);

				lastTime = millis();

				noInterrupts();
					measureAvailable = 0;
					errore 		= 0.5 - misuraSideIR(0); // 1=libero  0=vicino
					dLaterale   = errore;
				interrupts();

				updatePosition();
				
				// controllo sterzo da sensore laterale dx
				if ((statoRun == 1)||(statoRun == 3)){
					// a seconda dello stato attivo sensore DX o SX
					
					if (statoRun == 1) {
						digitalWrite( R_SIDE_FRONT, HIGH);
						digitalWrite( L_SIDE_FRONT,  LOW);
						raggiorSterzo =   kp*errore; // aggiunto in differenziale + S_NEUTRO; 
					}
					else{
						digitalWrite( R_SIDE_FRONT,  LOW);
						digitalWrite( L_SIDE_FRONT, HIGH);
						raggiorSterzo =  -kp*errore; // aggiunto in differenziale + S_NEUTRO; 
					}
					// errore +/- 0.5

					
					if (raggiorSterzo < -MAX_S) raggiorSterzo = -MAX_S;
					if (raggiorSterzo >  MAX_S) raggiorSterzo =  MAX_S;
				}
				
				if (statoRun == 2){
					motorSpeedRef = motorSpeedValue;
					direzione 	  = AVANTI;
				}

				// controllo sterzo da teta odometro
				/* stato 11 e 13 fanno si se si incontra  il sensore laterale
					il controllo passa a questo
				*/
				if ((statoRun == 4)||(statoRun == 11)||(statoRun == 13)){
					// Kp 1 ok
					// if teta > 3.14 -> teta -= 6.28
					// 0 - (6.27 - 6.28) = 0 - (-0.1) = atteso 0.1
					// 0 - 0.1  = - 0.1
					// 3.14 - 3.13 = 0.1
					// 3.14 - (3.15 - 6.28) = 6.27
					// if errore > 3.14 errore -= 6.28
					/* ID_001
					if (teta > 3.14) teta_ = teta - DUE_PI;
					else			 teta_ = teta;
					
					errore = tetaRef - teta_;
					if (errore > 3.14) errore -= DUE_PI;
					*/

					if (statoRun == 11) {
						digitalWrite( R_SIDE_FRONT,  LOW);
						digitalWrite( L_SIDE_FRONT, HIGH);
						
						if (errore >= 0.0){
							statoRun = 1; // 1=libero  0=vicino
						}
					}
					if (statoRun == 13){
						digitalWrite( R_SIDE_FRONT, HIGH);
						digitalWrite( L_SIDE_FRONT,  LOW);
						
						if (errore >= 0.0){
							statoRun = 3; // 1=libero  0=vicino
						}

					}
					
					// regolatore PI
					errore = tetaRef - teta;			// ID_001
					raggiorSterzo =   kpTeta*errore; 	// aggiunto in differenziale + S_NEUTRO; 
					i_part += raggiorSterzo*kiTeta;

					// anti windup
					// limito la parte integrale se la parte proporzionale è già alta
					// questo evita errore da scaricare
					// se la somma di parte P e I supera il massimo, la parte integrale viene
					// limitata a MAX - parte P
					if  ((raggiorSterzo + i_part) >  MAX_STERZO){
						i_part = MAX_STERZO - raggiorSterzo;
						if (i_part < 0) i_part = 0;
					}
					if  ((raggiorSterzo + i_part) < -MAX_STERZO){
						i_part = -MAX_STERZO - raggiorSterzo;	// -2 - (-1) = -1, -2 -(-3) = 1
						if (i_part > 0) i_part = 0;
					}
					if (i_part>  0.5) i_part =  0.5;
					if (i_part< -0.5) i_part = -0.5;
					
					raggiorSterzo += i_part;
					
					// errore +/- 0.5
					
					if (raggiorSterzo < -2.0) raggiorSterzo = -2.0;  	// ID_005
					if (raggiorSterzo >  2.0) raggiorSterzo =  2.0;		// ID_005
				}

				
				// R5 raggiunge nuovo teta ruotando su se stesso 
				if ((statoRun == 5)||(statoRun == 6)){

					errore = tetaRef -teta;
				
					switch (SM_R5){
						case 0:
								if ( teta < tetaRef ) SM_R5 = 1;	// salita
								if ( teta > tetaRef ) SM_R5 = 2;	// discesa
								if ( teta ==tetaRef ) {
									SM_R5     = 0;
									statoRun    = 0;  // senza rampa
									motorSpeed  = 0;  // annullo rampa
									motorSpeedRef = 0;
								}
							break;
							
						case 1:	// rampa salita
								motorSpeedRef =  108.0;
								direzione = AVANTI;
								
								// spazio di fermata 0.5*v*tf
								// 
				
								if (errore < delta_teta*7.0){
								// fermo
									SM_R5 		= 3;
									deltaS      = 10.8;
									/*
									statoRun    = 0;
									motorSpeed  = 0; 	// annullo rampa
									motorSpeedRef = 0;
									*/
								}
							break;
							
						case 2:	// rampa discesa

								motorSpeedRef =  108.0;
								direzione = INDIETRO;
								if (errore > delta_teta*7.0){
									// fermo
									SM_R5 		= 3;
									deltaS      = 10.8;
								}
							break;
							
						case 3:
								motorSpeedRef -= deltaS;
						
								if (motorSpeedRef< 0.0){
									SM_R5 		= 0;
									statoRun    = 0;	// senza rampa
									motorSpeed  = 0; 	// annullo rampa
									motorSpeedRef = 0;
								}
							break;
							
					
					}
				}// R5


				
				/* gestione raggiungimento target
				
						all'approccio si diminuisce la velocità
						alla partenza metto pwm alto per tot spazio per accertarmi di partire
						
						viaggio è lo spazio percorso dall'ultimo avvio
						l'avvio è quando cambia il riferimento di posizione
						nel primo tratto metto pwm alto
						passo a pwm moderato
						nell'approccio (E_APPROCCIO) metto pwm approccio
						se sono sotto E_posizionamento mi fermo
				
				*/
				// direzione


				if (((statoRun != 5)&&(statoRun != 6))&&(statoRun != 0)){
					if ( distanza > odometro )	direzione = AVANTI;
					else						direzione = INDIETRO;
					// gestione velocità
					// se viaggio 
					
						if ( abs(distanza - odometro) > E_APPROCCIO){
							motorSpeedRef = motorSpeedValue;
						}
						else
							if ( abs(distanza - odometro) > E_POSIZIONAMENTO){
								motorSpeedRef = APPROCCIO;
							}
							else{
								motorSpeedRef = FERMO;
								lastPosition  = odometro;
								statoRun      = 99;
							}
				}
				else{ // statoRun == 5 or 6 o zero (ruota su se stessa)
					;
				}
			}// fine parte temporizzata TEMPO_CONTROLLO ms

			if ((millis()-lastTimeFast) > 10){
				lastTimeFast = millis();

				if (statoRun == 99) motorSpeedRef = 0;
				
				// rampa sulla velocita'
				if (motorSpeedRef > motorSpeed)	motorSpeed += 2;
				if (motorSpeedRef < motorSpeed)	motorSpeed -= 4;	// 15

				if (motorSpeed > 250) motorSpeed = 250;
				if ((motorSpeed <   1)&&(statoRun == 99)){
					motorSpeed = 0;
					statoRun   = 0;
				}
			}// fine temporizzata veloce
			
			differenziale(motorSpeed);
	}
	
    if (mode == TEST_MOTORE){
        Serial.println("start TEST_MOTORE mode, enter motorSpeed, direzione");
		while (1){
			while (Serial.available() > 0) {

				// format x, y
				// look for the next valid integer in the incoming serial stream:
				motorSpeedRef = Serial.parseInt();
				// do it again:
				direzione = Serial.parseInt();
				
				//PDURATION = Serial.parseInt();
				
				// look for the newline. That's the end of your
				// sentence:
				if (Serial.read() == '\n') {
					// constrain the values to -50 - 50
			//                    x = constrain(x, -150, 150);
			//                    y = constrain(y, -200, 200);
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

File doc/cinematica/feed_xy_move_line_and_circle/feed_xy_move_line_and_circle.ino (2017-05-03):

#include <AccelStepper.h>
#include <MultiStepper.h>

#define RAD2DEG(_val) _val*180/PI
enum Verso{ CK, ACK};
enum Mode{ABS,REL};//modalità G0-1

int SXDIR = 6, SXSTEP = 7, DXDIR = 4, DXSTEP = 5, ENABLE = 3;

const float DEG = 0.1125;
const unsigned int DIAMETER = 72;
const unsigned int DELTAWHEEL = 172; //mm


//Arianna arianna(SXSTEP, SXDIR, DXSTEP, DXDIR, ENABLE);

#define DEBUG //for debug purprose
//PUBLIC
    int _DELTAWHEEL;
    float _STEPONMM;
//PRIVATE 
AccelStepper _SxMotor(AccelStepper::DRIVER,SXSTEP,SXDIR);//low to high transition make step
AccelStepper _DxMotor(AccelStepper::DRIVER,DXSTEP,DXDIR);
 MultiStepper _steppers;
    long _currentXposition;
    long _currentYposition;
    long _positions[2];
    float _currentAngle;
    //long _TOSTEP(float t);
    //int _STEPSX,_DIRSX,_STEPDX,_DIRDX,_ENABLE;
    float angleBetween();
    Mode mode;

void setupMotor(){
  _SxMotor.setMaxSpeed(500);//TODO manca funzione che lo fa
  _DxMotor.setMaxSpeed(500);
  _SxMotor.setAcceleration(200);
  _DxMotor.setAcceleration(200);
  
  //build the array (up to 10 stepper) that work toghter
  _steppers.addStepper(_SxMotor);
  _steppers.addStepper(_DxMotor);
  _positions[0] = 0;// la libreria usa cordinate assolute, in futuro si sistema
  _positions[1] = 0;
  pinMode(ENABLE,OUTPUT);
  digitalWrite(ENABLE,HIGH);

  
  _currentXposition=0;
  _currentYposition=0;
  _currentAngle=0;

  mode=ABS;
  }
void setup() {
  setupMotor();
  //da fare in una funz separata
  setGeometry(DEG, DIAMETER, DELTAWHEEL);
  Serial.begin(9600);
}

void loop() {
  int s;
  int d;
  float f;
  int8_t c;
  while (Serial.available() >= 2) {//ATTENZIONE la seriale e il codice viaggiano a velocità differenti, da ora in poi ogni riga dovrà avere un minimo di 2 byte
    c = Serial.read();
    switch (c) {
      case 'M':
        switch (Serial.parseInt()) {
          case 114:
            Serial.print(F("Current position: ")); Serial.print((long)(getCurrentPosition())[0]); Serial.print(F(" ")); Serial.println((long)(getCurrentPosition())[1]);
            break;
          case 115:
            Serial.print(F("Current angle: ")); Serial.println(getCurrentAngle());
        } 
        break;
      case 'G':
        switch (Serial.parseInt()) {
          case 0:
          case 1:
            s = Serial.parseInt(); //delta x
            d = Serial.parseInt(); //delta y
            if(mode==ABS)//di default è assoluto, guardare setup 
              move(s, d,_currentAngle,&_currentXposition,&_currentYposition);//chiamata all'assoluto
            else if(mode==REL)
              move(s,d,0);//chiama al relativo
            break;
           case 90: Serial.println(F("Setted to absolute position"));
            mode=ABS;
            break;
           case 91: Serial.println(F("Setted to relative position"));
            mode=REL;
            break;
        }

        break;
      case 'l': s=Serial.parseInt(); line(s);//feed mm
        break;
      case 'c': c = Serial.read();
#ifdef DEBUG
        Serial.println(c);
#endif
        f = Serial.parseFloat();
        s = Serial.parseInt();
        if (c == 99) { //ca 90 30 per eseguire una rotazione a sinistra (anticlockwise) di 90 gradi con la ruota sinistra che esegue una circonferenza con centro distante 30 mm
          //TODO BUG there is no assumption with the order of the parseInt and parseFloat, please notify TODO TODO in this function circle(Serial.parseFloat(),Serial.parseInt(),174,positions,Verso::ACK);
          circle(f, s, CK); //feed mm,verso orario //TODO cambiare con const
        } else if (c == 'a') {
          circle(f, s, ACK); //verso antiorario
        }
        break;
      default: Serial.print(F("NON compriendo"));// Serial.flush();
    }

  }
}

void setGeometry(float resolutionOfOneStepInDeg, uint16_t diameterOfWheel, uint16_t  distanceBetweenWheel){
  _STEPONMM=(360/resolutionOfOneStepInDeg)/((float)diameterOfWheel*PI);
  _DELTAWHEEL=distanceBetweenWheel;
}

void circle(float alpha,long r0, Verso v){
  _circle(alpha,r0,v);
  _setDistance();
  runToDistance();
}
void line(long p){
  _line(p);//TODO inserire linee di debug
  _setDistance();
  runToDistance();
}
void move(long x, long y,float angolo,long * currX, long * currY){
  //_positions[0]+=_TOSTEP(x);
  //_positions[1]+=_TOSTEP(y);
  long dX,dY;
  dX=x-*currX;
  dY=y-*currY;
  //TODO REFACTORING CODICE COMUNE
  //http://www.nongnu.org/avr-libc/user-manual/group__avr__math.html
  /*

double atan2  ( double  __y,
double  __x 
)   
The atan2() function computes the principal value of the arc tangent of __y / __x
, using the signs of both arguments to determine the quadrant of the return value. 
The returned value is in the range [-pi, +pi] radians.
  */
  float toAngle = RAD2DEG(atan2(dY,dX));
  float eps = toAngle - angolo;
  _currentAngle=toAngle;
  *currX=x;
  *currY=y;
  
  circle(eps,0,ACK);
  /*if(eps>0)
    cirlce(fabs(eps),0,ACK); //TODO a sinistra andrà bene
  else
    circle(fabs(eps),0,CK); //TODO ERRORE a destra giro intorno alla ruota destra, ERRORE
  */
  line(sqrt(dX*dX + dY*dY));
}

//movimento relativo, non ho bisogno della posizione attuale
void move(long x, long y,float angolo){
  //_positions[0]+=_TOSTEP(x);
  //_positions[1]+=_TOSTEP(y);
  long dX,dY;
  dX=x;
  dY=y;
  
  //http://www.nongnu.org/avr-libc/user-manual/group__avr__math.html
  /*

double atan2  ( double  __y,
double  __x 
)   
The atan2() function computes the principal value of the arc tangent of __y / __x
, using the signs of both arguments to determine the quadrant of the return value. 
The returned value is in the range [-pi, +pi] radians.
  */
  float toAngle = RAD2DEG(atan2(dY,dX));
  circle(angolo,0,ACK);
  /*if(eps>0)
    cirlce(fabs(eps),0,ACK); //TODO a sinistra andrà bene
  else
    circle(fabs(eps),0,CK); //TODO ERRORE a destra giro intorno alla ruota destra, ERRORE
  */
  line(sqrt(dX*dX + dY*dY));
}
void runToDistance(){
  _steppers.runSpeedToPosition();
}

long* getCurrentPosition(){//TODO da sistemare in mm assoluti
  /*long ar[2];
  ar[0]=_currentXposition;
  ar[1]=_currentYposition;
  return ar;*/
  return _positions;
}
float getCurrentAngle(){
  return _currentAngle;
}
 /*
}
4rianna::runSingleStep(){
  _steppers.runSpeedToPosition();
}
*/

 /*
4rianna::stepBeforeTarget(){
  
}
*/
long _TOSTEP(long t){
  return t*_STEPONMM;
}


void _setDistance(){
  _steppers.moveTo(_positions);
}

void _line(long _pos){
  #ifdef DEBUG
  Serial.print("Pianifico linea di:");
  Serial.print(_STEPONMM*_pos);
  Serial.println(" step.");
  #endif

     _positions[0]+=_STEPONMM*_pos;
    _positions[1]+=_STEPONMM*_pos;
                
}
//s1 è lo spazioe seguito dalla ruota sinistra :
//nel caso di verso antiorario positivo il centro della circonferenza è a sinistra della ruota sinistra (il roboto gira verso sinistra)
//nel caso negativo gira a destra (il centro della circonferenza seguita dalla ruota è verso il centro del robot, a destra della ruota sinistra)
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

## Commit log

2017-04-20 creazinoe folder, README e upload sketch per la gestione via seriale di 4rianna
2017-04-20 creazione folder, README e upload sketch per la gestione via seriale di 4rianna
2017-09-20 aggiornamento cartelle
    [Component2.stl, UMBmarkTest_ari02.xlsx, UMBmarkTest_ari03.xlsx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]
2018-12-16 il progetto è stato portato in: https://github.com/giorgio323323/ARI_V3
